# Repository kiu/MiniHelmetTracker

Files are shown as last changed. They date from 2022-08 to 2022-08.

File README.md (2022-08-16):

# MiniHelmetTracker

*MiniHelmetTracker* is a real-time standings table robot.

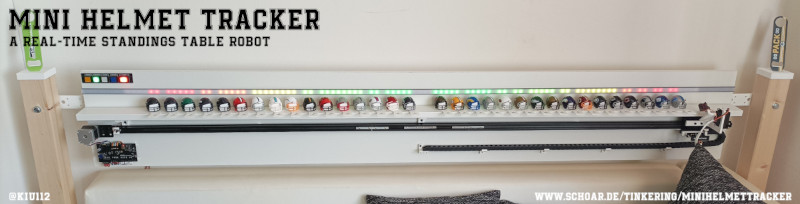
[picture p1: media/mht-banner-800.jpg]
MHT

 
*MiniHelmetTracker* retrieves standings data - close to real-time - via WiFi and sorts [mini helmets](https://www.amazon.de/Riddell-8056173-NFL-32-teiliges-Helm-Tracker-Set/dp/B088W86SX4/) by league, conference, division or playoffs. A physical representation of the well known standings tables from [NFL](https://www.espn.com/nfl/standings) or [ESPN](https://www.espn.com/nfl/standings).

Checkout the [full story](https://schoar.de/tinkering/MiniHelmetTracker) or explore this repository including STL files, schematics, PCB layouts, firmware, server, etc.

# Youtube

MHT Video (https://youtu.be/LY5VMEqtx_c "MHT Video")

MHT Making (https://youtu.be/Ac1G4HAgR_Y "MHT Making")

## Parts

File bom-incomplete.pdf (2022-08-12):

BOM

Page 1

Symbol | Description | Req | +VAT | Price | Price (sum) | Provider | ID
| | | | MOQ 1
Electrical
- | TMC2209 Module | 1 | 0 | 4,94 € | 4,94 € | https://aliexpress.com | 33029587820
- | ESP8266 Module | 1 | 0 | 6,49 € | 6,49 € | https://amazon.de | B078J7LDLY
- | Power Supply 5V/12V 65W (totally overpowered) | 1 | 0 | 20,87 € | 20,87 € | https://reichelt.de | SNT RD 65A
- | Power Supply Protection | 1 | 0 | 0,44 € | 0,44 € | https://reichelt.de | TBC-07
- | Power Cord 3m | 1 | 0 | 3,90 € | 3,90 € | https://reichelt.de | NKS 300 WS
- | NEMA 17 17HS4401 | 1 | 0 | 10,96 € | 10,96 € | https://amazon.de | B07GLKQYWJ
- | Limit Switch | 1 | 0 | 2,77 € | 2,77 € | https://aliexpress.com | 1005003536527857
- | LED strip RGB APA102 60/m | 2 | 0 | 9,02 € | 18,04 € | https://aliexpress.com | 1005002583856530
| Button Square | 4 | 0 | 2,07 € | 8,28 € | https://aliexpress.com | 32886794895
| Button Rectangle | 1 | 0 | 2,06 € | 2,06 € | https://aliexpress.com | 32871885629
Mechanical
- | LED strip mount 2000x17x7 | 1 | 0 | 19,97 € | 19,97 € | https://amazon.de | B07549D36V
- | Cable Chain 10x10 (2m) | 2 | 0 | 8,06 € | 16,12 € | https://aliexpress.com | 1005001795469984
- | 2020 V-Profile 800mm | 2 | 0 | 8,57 € | 17,14 € | https://aliexpress.com | 32956797126
- | 2020 V-Profile 300mm | 1 | 0 | 5,42 € | 5,42 € | https://aliexpress.com | 32956797126
- | (4x) Pofile Connector | 2 | 0 | 5,59 € | 11,18 € | https://aliexpress.com | 33014820100
- | NEMA 17 Mounting Plate | 1 | 0 | 2,61 € | 2,61 € | https://aliexpress.com | 33012021651
- | Belt Tensioner | 1 | 0 | 6,41 € | 6,41 € | https://aliexpress.com | 4000598324722
- | GT2 Belt 5m 6mm | 1 | 0 | 4,73 € | 4,73 € | https://aliexpress.com | 32882998299
- | 2020 V-Profile gantry | 1 | 0 | 7,95 € | 7,95 € | https://aliexpress.com | 4000177053846
- | Pulley 20T W6 B4 | 1 | 0 | 1,45 € | 1,45 € | https://aliexpress.com | 4001058371220
- | Servo MG996R | 1 | 0 | 12,89 € | 12,89 € | https://amazon.de | B088NJRFD7
- | Servo MG90S | 1 | 0 | 6,89 € | 6,89 € | https://amazon.de | B095YXMG3F
Misc
- | Mini Helmet Set | 1 | 0 | 47,92 € | 47,92 € | https://amazon.de | B088W86SX4
- | Wood 2000x300x16 | 1 | 0 | 10,99 € | 10,99 € | https://obi.de | 6848618
- | Wood 70x70x2100 | 2 | 0 | 25,17 € | 50,34 € | https://obi.de | 6870299
- | Wood 58x16x2400 | 1 | 0 | 13,99 € | 13,99 € | https://obi.de | 7930035
- | PCB + Shipping jlcpcb.com | 1 | 0 | 58,11 € | 58,11 € | https://jlcpcb.com | -
- | Shipping reichelt.de | 1 | 0 | 5,95 € | 5,95 € | https://reichelt.de | -

SUM
378,81 €
378,81 €

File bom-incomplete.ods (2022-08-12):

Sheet: BOM
Symbol | Description | Req | +VAT | Price | Price (sum) | Provider | ID
 |  |  |  | MOQ | 1
Electrical
- | TMC2209 Module | 1 | 0 | 4,94 € | 4,94 € | https://aliexpress.com | 33029587820
- | ESP8266 Module | 1 | 0 | 6,49 € | 6,49 € | https://amazon.de | B078J7LDLY
- | Power Supply 5V/12V 65W (totally overpowered) | 1 | 0 | 20,87 € | 20,87 € | https://reichelt.de | SNT RD 65A
- | Power Supply Protection | 1 | 0 | 0,44 € | 0,44 € | https://reichelt.de | TBC-07
- | Power Cord 3m | 1 | 0 | 3,90 € | 3,90 € | https://reichelt.de | NKS 300 WS
- | NEMA 17 17HS4401 | 1 | 0 | 10,96 € | 10,96 € | https://amazon.de | B07GLKQYWJ
- | Limit Switch | 1 | 0 | 2,77 € | 2,77 € | https://aliexpress.com | 1005003536527857
- | LED strip RGB APA102 60/m | 2 | 0 | 9,02 € | 18,04 € | https://aliexpress.com | 1005002583856530
 | Button Square | 4 | 0 | 2,07 € | 8,28 € | https://aliexpress.com | 32886794895
 | Button Rectangle | 1 | 0 | 2,06 € | 2,06 € | https://aliexpress.com | 32871885629
Mechanical
- | LED strip mount 2000x17x7 | 1 | 0 | 19,97 € | 19,97 € | https://amazon.de | B07549D36V
- | Cable Chain 10x10 (2m) | 2 | 0 | 8,06 € | 16,12 € | https://aliexpress.com | 1005001795469984
- | 2020 V-Profile 800mm | 2 | 0 | 8,57 € | 17,14 € | https://aliexpress.com | 32956797126
- | 2020 V-Profile 300mm | 1 | 0 | 5,42 € | 5,42 € | https://aliexpress.com | 32956797126
- | (4x) Pofile Connector | 2 | 0 | 5,59 € | 11,18 € | https://aliexpress.com | 33014820100
- | NEMA 17 Mounting Plate | 1 | 0 | 2,61 € | 2,61 € | https://aliexpress.com | 33012021651
- | Belt Tensioner | 1 | 0 | 6,41 € | 6,41 € | https://aliexpress.com | 4000598324722
- | GT2 Belt 5m 6mm | 1 | 0 | 4,73 € | 4,73 € | https://aliexpress.com | 32882998299
- | 2020 V-Profile gantry | 1 | 0 | 7,95 € | 7,95 € | https://aliexpress.com | 4000177053846
- | Pulley 20T W6 B4 | 1 | 0 | 1,45 € | 1,45 € | https://aliexpress.com | 4001058371220
- | Servo MG996R | 1 | 0 | 12,89 € | 12,89 € | https://amazon.de | B088NJRFD7
- | Servo MG90S | 1 | 0 | 6,89 € | 6,89 € | https://amazon.de | B095YXMG3F
Misc
- | Mini Helmet Set | 1 | 0 | 47,92 € | 47,92 € | https://amazon.de | B088W86SX4
- | Wood 2000x300x16 | 1 | 0 | 10,99 € | 10,99 € | https://obi.de | 6848618
- | Wood 70x70x2100 | 2 | 0 | 25,17 € | 50,34 € | https://obi.de | 6870299
- | Wood 58x16x2400 | 1 | 0 | 13,99 € | 13,99 € | https://obi.de | 7930035
- | PCB + Shipping jlcpcb.com | 1 | 0 | 58,11 € | 58,11 € | https://jlcpcb.com | -
- | Shipping reichelt.de | 1 | 0 | 5,95 € | 5,95 € | https://reichelt.de | -
 |  |  |  |  | SUM
 |  |  |  |  | 378,81 €
 |  |  |  |  | 378,81 €

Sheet: BOM_2
Symbol | Description | Req | +VAT | Price | Price (sum) | Provider | ID
 |  |  |  | MOQ | 1
Electronic / Base
 | ATMEGA 328PB-AU | 1 | 0 | 1,44 € | 1,44 € | http://reichelt.de | ATMEGA 328PB-AU
 | LDO 5V >=200mA | 1 | 0 | 0,36 € | 0,36 € | http://reichelt.de | NCP 1117 ST50T3G
 | NPN Transitor >=100mA | 1 | 0 | 0,02 € | 0,02 € | http://reichelt.de | BC 847C SMD
 | Diode | 1 | 0 | 0,02 € | 0,02 € | http://reichelt.de | BAV 99 SMD
 | 10uF/25V Tantalum D | 2 | 0 | 0,35 € | 0,70 € | http://reichelt.de | TAJ 7343 10/25
 | 100nF 0805 | 3 | 0 | 0,05 € | 0,15 € | http://reichelt.de | KEM X7R0805 100N
 | 10k 0805 | 3 | 0 | 0,02 € | 0,06 € | http://reichelt.de | RND 0805 1 10K
 | 1k 0805 | 1 | 0 | 0,02 € | 0,02 € | http://reichelt.de | RND 0805 1 1,0K
 | Relay 5V | 1 | 0 | 2,60 € | 2,60 € | http://reichelt.de | G2RL-24 DC5
 | 1x05 Pin Header with cable | 2 | 0 | 0,67 € | 1,34 € | http://reichelt.de | PS 25/5G BR
 | Terminal 1x02 5.08 | 2 | 0 | 0,25 € | 0,50 € | http://reichelt.de | CTB0509-2
 | Header 2x03 2.54 | 1 | 0 | 0,25 € | 0,25 € | http://reichelt.de | WSL 6G
 | Header 1x02 2.54 | 1 | 0 | 0,05 € | 0,05 € | http://reichelt.de | MPE 087-1-002
 | Header 1x03 2.54 | 1 | 0 | 0,08 € | 0,08 € | http://reichelt.de | MPE 087-1-003
 | Socket 1x05 2.54 | 1 | 0 | 0,23 € | 0,23 € | http://reichelt.de | MPE 094-1-005
 | Socket 1x04 2.54 | 1 | 0 | 0,17 € | 0,17 € | http://reichelt.de | MPE 094-1-004
Electronic / Gantry
 | ATMEGA 328PB-AU | 1 | 0 | 1,44 € | 1,44 € | http://reichelt.de | ATMEGA 328PB-AU
 | LDO 5V >=200mA | 1 | 0 | 0,36 € | 0,36 € | http://reichelt.de | NCP 1117 ST50T3G
 | NPN Transitor >=100mA | 1 | 0 | 0,02 € | 0,02 € | http://reichelt.de | BC 847C SMD
 | Diode | 1 | 0 | 0,02 € | 0,02 € | http://reichelt.de | BAV 99 SMD
 | 10uF/25V Tantalum D | 2 | 0 | 0,35 € | 0,70 € | http://reichelt.de | TAJ 7343 10/25
 | Belt Tensioner | 1
 | T-Nut M4 (?) | 4
 | M4x?? | 4
 | GT2 Belt 5m | 1
Electronic / Control
Electrical
 | Power Supply 1x5V 1x12V | 1
 | Power Supply Protection | 1
 | Power Cord | 1
 | Cable Chain 10x10 (3m) | 3
Mechanical
 | 2020 V-Profile 800mm | 2
 | 2020 V-Profile 400mm | 1
 | Pofile Connector (4) | 4
 | NEMA 17 Mounting Plate | 1
 | Belt Tensioner | 1
 | T-Nut M4 (?) | 4
 | M4x?? | 4
 | GT2 Belt 5m | 1
 | Gantry | 1
- | Power Supply 15V >=2A | 1 | 0 | 11,07 € | 11,07 € | http://reichelt.de | MW LRS-35-15
- | Power Supply Protection | 1 | 0 | 0,34 € | 0,34 € | http://reichelt.de | TBC-05
- | Case 167x125x82mm | 1 | 0 | 10,10 € | 10,10 € | http://reichelt.de | HNS 12516782-H01
- | Cable 2x0,75mm 5m | 1 | 0 | 1,30 € | 1,30 € | http://reichelt.de | LAT 275-5
- | Connector | 1 | 0 | 1,30 € | 1,30 € | http://reichelt.de | DELOCK 65421
- | Separator M3 10mm | 2 | 0 | 0,11 € | 0,22 € | http://reichelt.de | DI 10MM
- | Separator M4 5mm | 3 | 0 | 0,09 € | 0,27 € | http://reichelt.de | VT DKM 5MM
- | Cable Gland M16 | 2 | 0 | 0,25 € | 0,50 € | http://reichelt.de | MBF 16
- | Cable Gland M16 Fix | 2 | 0 | 0,10 € | 0,20 € | http://reichelt.de | MGM 16
- | Aderendhülsen 0,75mm | 1 | 0 | 1,03 € | 1,03 € | http://reichelt.de | VT AEHI 0,75-100
- | Shipping reichelt.de | 1 | 0 | 5,95 € | 5,95 € | http://reichelt.de | -
Misc
(JHTU21) | GY-21 HTU21 Temperature Module | 1 | 0 | 5,99 € | 5,99 € | http://amazon.de | B07V9PJP1K
(JRTC1) | DS3231 RTC Module | 1 | 0 | 10,89 € | 10,89 € | http://amazon.de | B07QW2D4NF
- | Screw M3x5 | 4 | 0 | 0,00 € | 0,00 € | - | -
- | Screw M4x14 | 3 | 0 | 0,00 € | 0,00 € | - | -
(JNOW1, JWAIT1) | Push Button, 19mm, LED Red + Blue | 2 | 0 | 3,60 € | 7,20 € | http://aliexpress.com | 1005002351204813
- | PCB 138x85 + Stencil + Shipping + VAT | 1 | 0 | 37,33 € | 37,33 € | http://jlcpcb.com | -
 |  |  |  |  | SUM
 |  |  |  |  | 104,22 €
 |  |  |  |  | 104,22 €

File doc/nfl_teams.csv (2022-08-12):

ID | Name | Abbreviation | Conference | Division
1 | Arizona Cardinals | ARI | NFC | West
2 | Atlanta Falcons | ATL | NFC | South
3 | Baltimore Ravens | BAL | AFC | North
4 | Buffalo Bills | BUF | AFC | East
5 | Carolina Panthers | CAR | NFC | South
6 | Chicago Bears | CHI | NFC | North
7 | Cincinnati Bengals | CIN | AFC | North
8 | Cleveland Browns | CLE | AFC | North
9 | Dallas Cowboys | DAL | NFC | East
10 | Denver Broncos | DEN | AFC | West
11 | Detroit Lions | DET | NFC | North
12 | Green Bay Packers | GB | NFC | North
13 | Houston Texans | HOU | AFC | South
14 | Indianapolis Colts | IND | AFC | South
15 | Jacksonville Jaguars | JAX | AFC | South
16 | Kansas City Chiefs | KC | AFC | West
17 | Miami Dolphins | MIA | AFC | East
18 | Minnesota Vikings | MIN | NFC | North
19 | New England Patriots | NE | AFC | East
20 | New Orleans Saints | NO | NFC | South
21 | NY Giants | NYG | NFC | East
22 | NY Jets | NYJ | AFC | East
23 | Las Vegas Raiders | LV | AFC | West
24 | Philadelphia Eagles | PHI | NFC | East
25 | Pittsburgh Steelers | PIT | AFC | North
26 | Los Angeles Chargers | LAC | AFC | West
27 | San Francisco 49ers | SF | NFC | West
28 | Seattle Seahawks | SEA | NFC | West
29 | Los Angeles Rams | LAR | NFC | West
30 | Tampa Bay Buccaneers | TB | NFC | South
31 | Tennessee Titans | TEN | AFC | South
32 | Washington Football Team | WAS | NFC | East

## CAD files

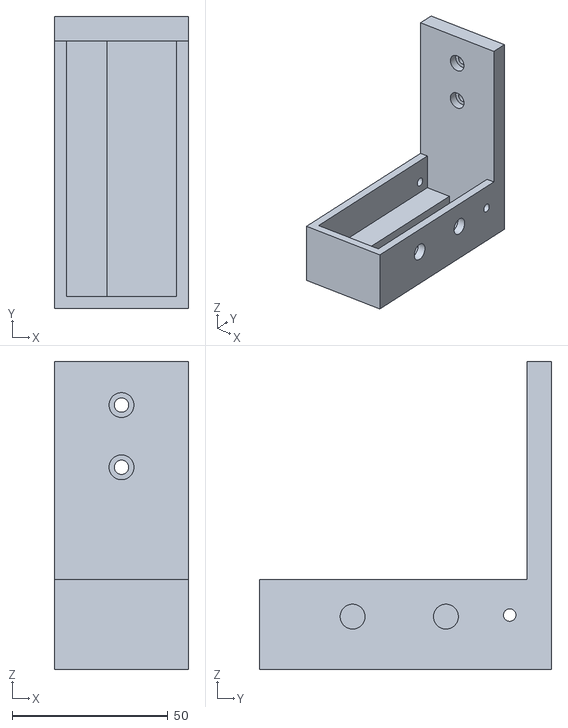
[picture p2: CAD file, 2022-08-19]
mech/mount-meanwell-35W.stl
43.2 x 94.0 x 99.0

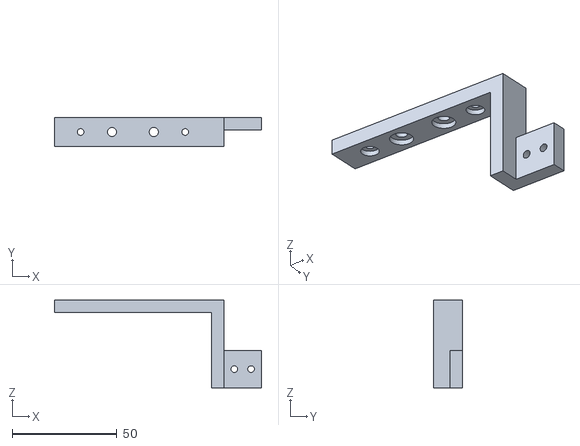
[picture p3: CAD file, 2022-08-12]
mech/chain-end.stl
99.0 x 14.0 x 42.0

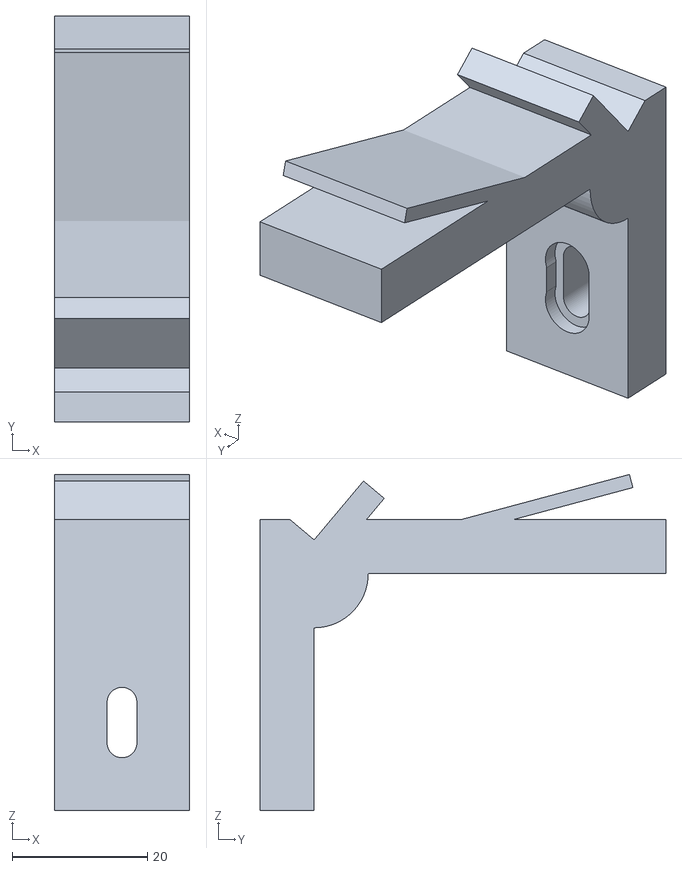
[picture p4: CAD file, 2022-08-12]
mech/mount-plate_3x.stl
20.0 x 60.0 x 49.7

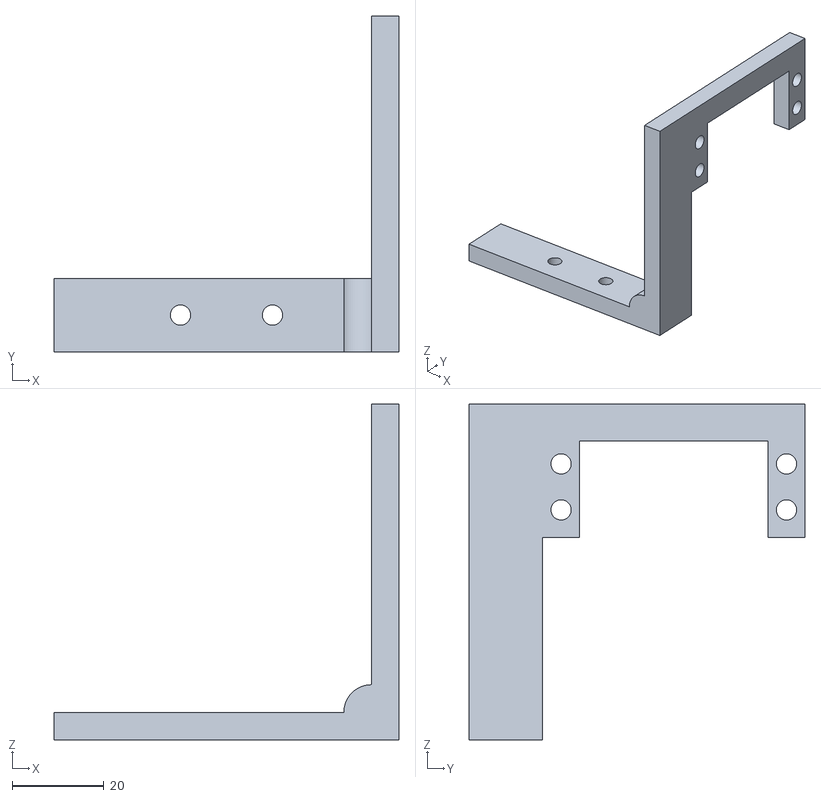
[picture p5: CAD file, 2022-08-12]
mech/mount-servo.stl
75.0 x 73.0 x 73.0

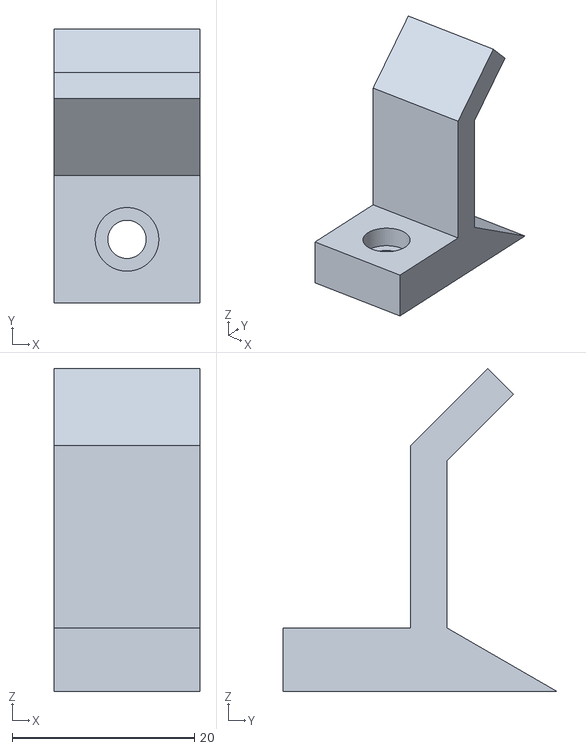
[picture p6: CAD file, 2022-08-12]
mech/chain-middle_4x.stl
16.0 x 30.1 x 35.5

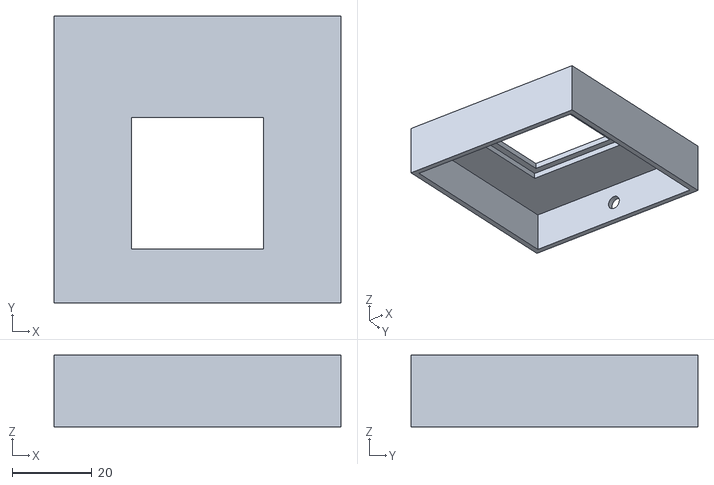
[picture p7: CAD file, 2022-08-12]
mech/mount-opener-base_2x.stl
72.0 x 72.0 x 18.0

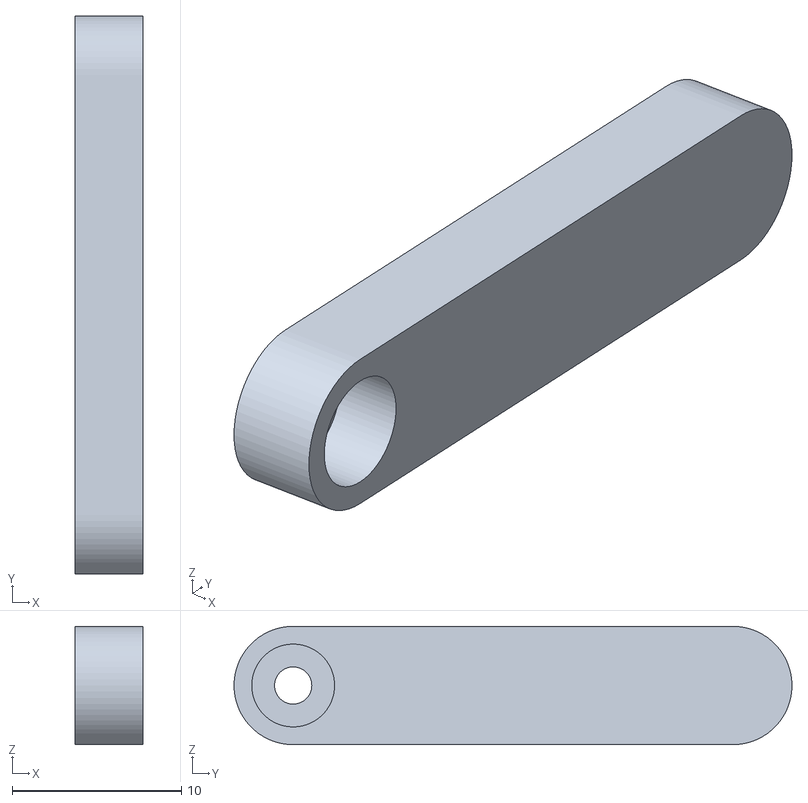
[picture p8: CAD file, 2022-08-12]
mech/helmet-horn.stl
4.00 x 33.0 x 7.00

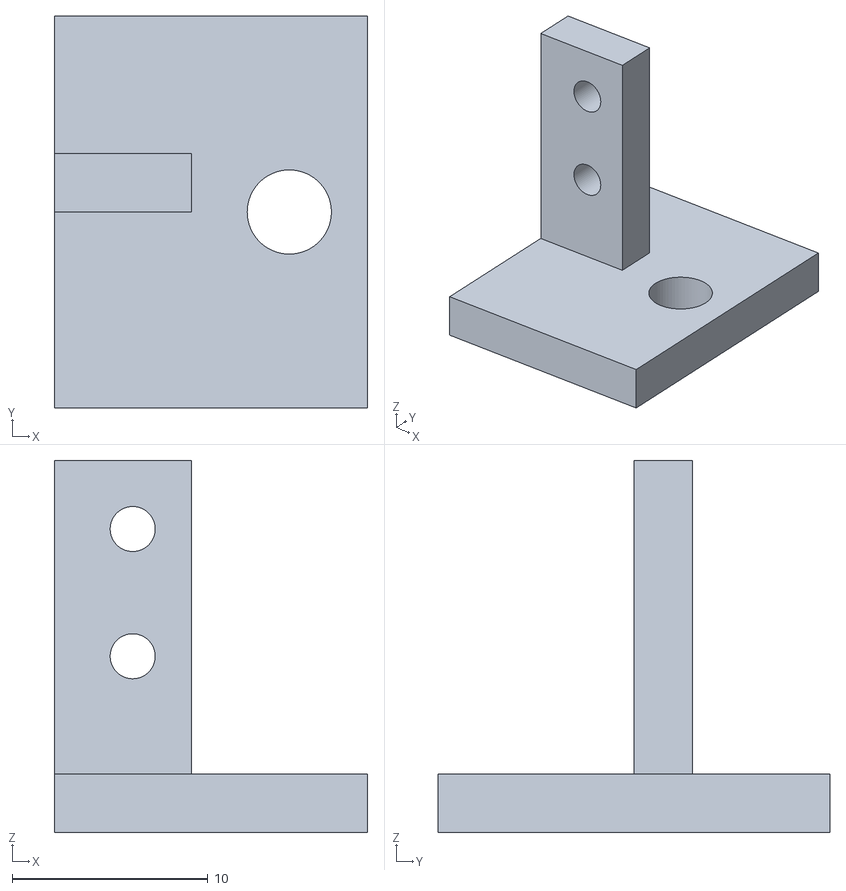
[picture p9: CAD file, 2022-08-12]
mech/mount-limit_switch.stl
16.0 x 20.0 x 19.0

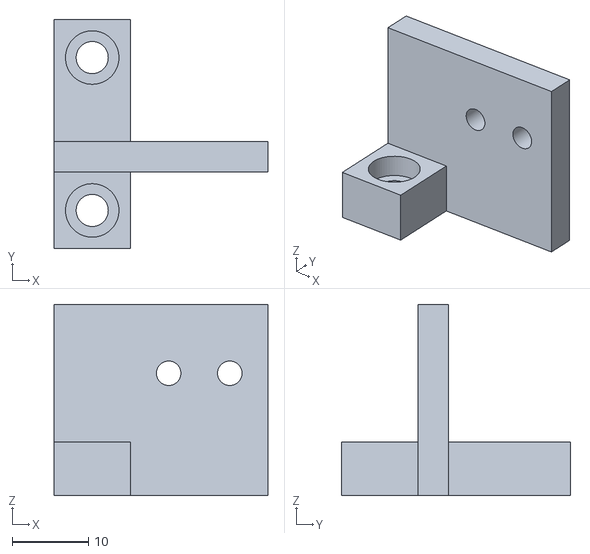
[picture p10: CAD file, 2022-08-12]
mech/chain-start.stl
28.0 x 30.0 x 25.0

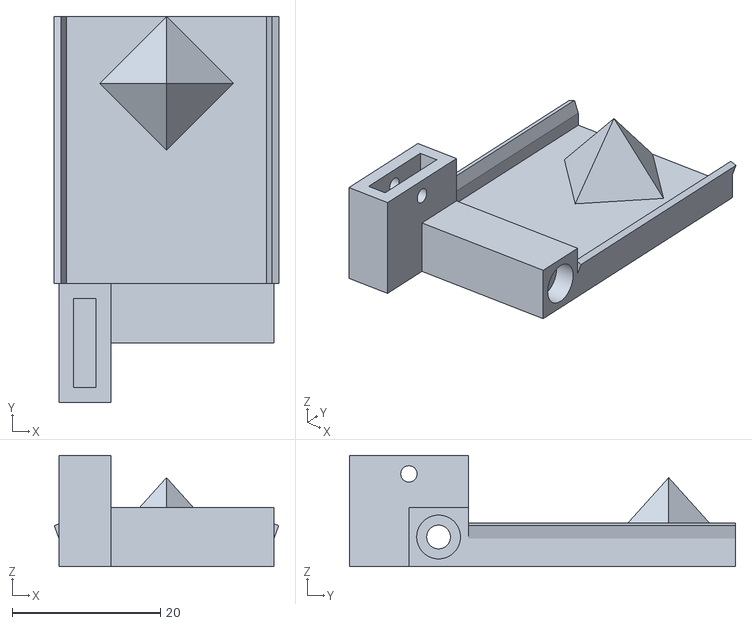
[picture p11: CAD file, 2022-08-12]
mech/helmet-receptacle.stl
30.2 x 52.0 x 15.0

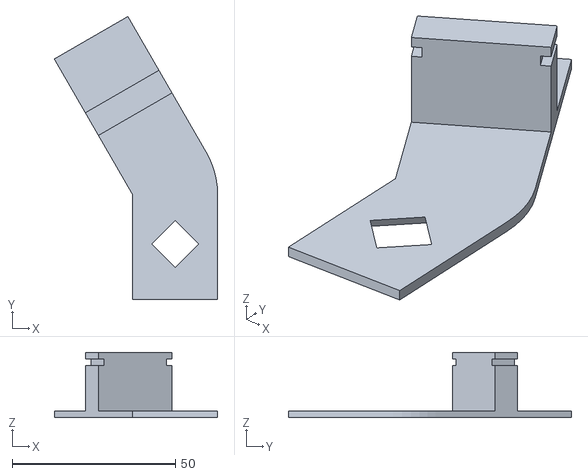
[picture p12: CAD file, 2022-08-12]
mech/helmet-holder_32x.stl
50.0 x 86.6 x 20.0

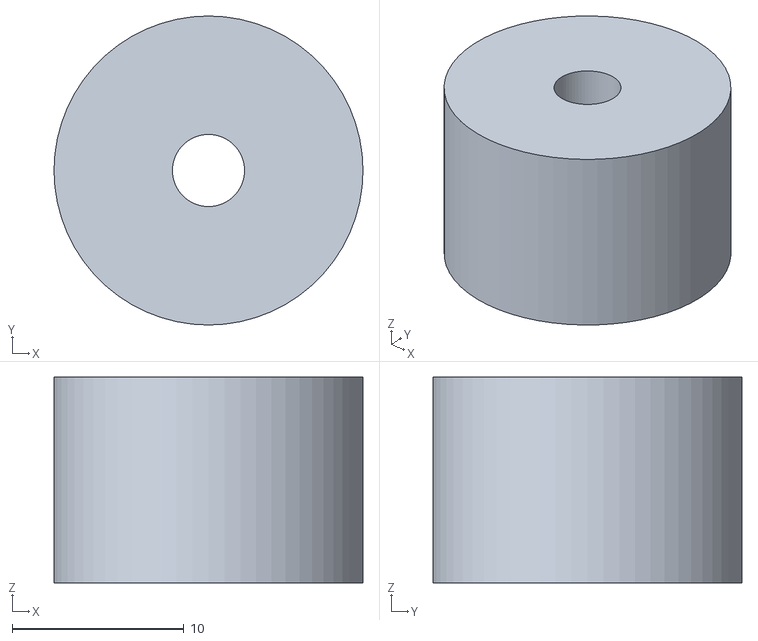
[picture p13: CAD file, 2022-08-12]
mech/mount-rail_2x.stl
18.0 x 18.0 x 12.0

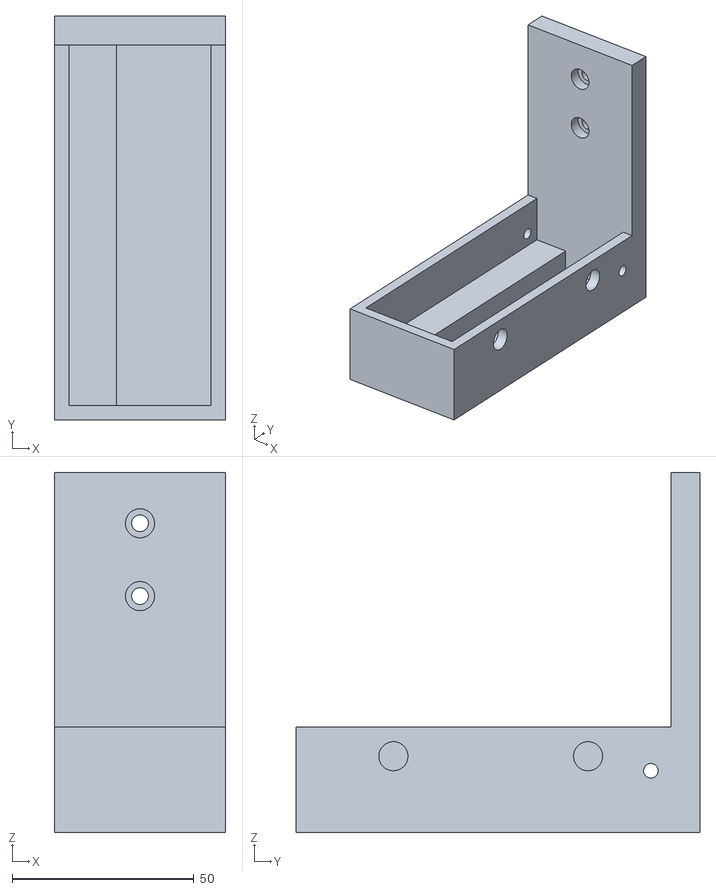
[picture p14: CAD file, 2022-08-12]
mech/mount-meanwell.stl
47.0 x 111.0 x 99.0

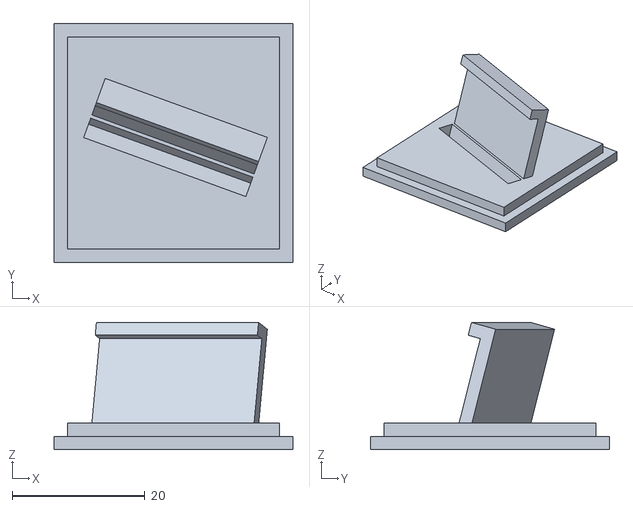
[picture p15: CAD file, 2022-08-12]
mech/mount-opener-right.stl
36.0 x 36.0 x 19.2

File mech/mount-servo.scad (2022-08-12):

$fn = 60;

//--------------------------------------------------------

	  w = 75;
	  b = 16;
	  difference() {
			cube([w, b, 6]);
			translate([w/2 - 20 / 2, b/2, 0]) cylinder(h=6, d=4.4);
			translate([w/2 - 20 / 2, b/2, 0]) cylinder(h=2, d=9);
			
			translate([w/2 + 20 / 2, b/2, 0]) cylinder(h=6, d=4.4);
			translate([w/2 + 20 / 2, b/2, 0]) cylinder(h=2, d=9);
	  }
	  
	  translate([w - 6, 0, 0]) cube([6, b, 6 + 50-11+29-1]);
	  translate([w - 6, b/2, 6]) rotate([90, 0, 0]) cylinder(h = b, d = 12, center = true);

translate([75, 0+16, 6 + 50+29-11-1]) rotate([-90, 0, 90]) difference() {
	  cube([41+16, 21+8, 6]);
	  translate([8, 8, 0]) cube([41, 21, 6]);
	  translate([4, 8+5, 0]) cylinder(h=6, d=4.4);
	  translate([4, 8++5+10, 0]) cylinder(h=6, d=4.4);
	  translate([41 + 8 + 4, 8+5, 0]) cylinder(h=6, d=4.4);
	  translate([41 + 8 + 4, 8+5+10, 0]) cylinder(h=6, d=4.4);
}

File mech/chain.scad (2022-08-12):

$fn = 60;

//--------------------------------------------------------

translate([0, 0, 0]) start();
translate([40, 0, 0]) middle();
translate([80, 0, 0]) end();

//--------------------------------------------------------

module start() {
	  difference() {
			cube([10, 30, 7]);
			translate([10/2, 10/2, 0]) cylinder(h=7, d=4.2);
			translate([10/2, 10/2, 4]) cylinder(h=3, d=7);

			translate([10/2, 30-10/2, 0]) cylinder(h=7, d=4.2);
			translate([10/2, 30-10/2, 4]) cylinder(h=7, d=7);
	  }


	  translate([0, 10 + 4, 0]) rotate([90, 0, 0]) difference() {
			cube([10+18, 18+7, 4]);
			translate([10 + 5, 18/2+7, 0]) cylinder(h=4, d=3.2);
			translate([10 + 5 + 8, 18/2+7, 0]) cylinder(h=4, d=3.2);
	  }
}

module middle() {
	  difference() {
			cube([16, 32, 7]);
			translate([0, 12.8, 10]) rotate([-30, 0, 0]) cube([30, 30, 30]);
			translate([16/2, 7, 0]) cylinder(h=7, d=4.2);
			translate([16/2, 7, 4]) cylinder(h=3, d=7);
	  }
	  
	  translate([0, 18 - 4, 7]) cube([16, 4, 20]);
	  translate([0, 18 - 4, 27]) rotate([-45, 0, 0]) cube([16, 4, 12]);
}

module end() {
	  w = 75;
	  difference() {
			cube([w, 14, 6]);
			translate([w/2 - 20 / 2, 14/2, 0]) cylinder(h=6, d=4.4);
			translate([w/2 - 20 / 2, 14/2, 0]) cylinder(h=2, d=9);
			
			translate([w/2 + 20 / 2, 14/2, 0]) cylinder(h=6, d=4.4);
			translate([w/2 + 20 / 2, 14/2, 0]) cylinder(h=2, d=9);

			translate([w/2 - 50 / 2, 14/2, 0]) cylinder(h=6, d=3.2);
			translate([w/2 - 50 / 2, 14/2, 0]) cylinder(h=2, d=7);
			translate([w/2 + 50 / 2, 14/2, 0]) cylinder(h=6, d=3.2);
			translate([w/2 + 50 / 2, 14/2, 0]) cylinder(h=2, d=7);
	  }

	  d = 36;
	  
	  translate([w, 0, -d]) cube([6, 14, d+6]);
	  
	  translate([w + 6, 14, -d]) rotate([90, 0, 0]) difference() {
			cube([18, 18, 6]);
			translate([5, 18/2, 0]) cylinder(h=6, d=3.2);
			translate([5, 18/2, 0]) cylinder(h=2, d=6);
			translate([5 + 8, 18/2, 0]) cylinder(h=6, d=3.2);
			translate([5 + 8, 18/2, 0]) cylinder(h=2, d=6);
	  }
}

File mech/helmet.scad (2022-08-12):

$fn = 60;

base_thick = 2.0;
holder_width = 26.0;
recept_width = holder_width + 1 + 2;

height = 18;

//--------------------------------------------------------

grab();
translate ([1.5, 18, 2]) holder();
translate ([recept_width/2 - 4/2, 0, 20]) rotate([0, 90, 0]) horn();

//--------------------------------------------------------
module grab() {
	  rotate([0, 90, 0]) translate([-8, 0, 0]) servo_mount_big();	  
	  translate([0, 8, 8]) rotate([90, 0, 0]) servo_mount_small();
	  translate([0, -8, 0]) cube([7, 8, 8]);
	  translate([0, 8, 0]) receptacle();
}

//--------------------------------------------------------

module servo_mount_small() {
	  difference() {
			cube([7, 7, 16]);
			translate([2, 2, 2]) cube([3, 5, 12]);
			translate([7/2, 5/2 + 2, 16 / 2]) rotate([0, 90, 0]) cylinder(h=7, d=2.2, center = true);
	  }
}

//--------------------------------------------------------

module servo_mount_big() {
	  servo_height = recept_width;
	  servo_gear = 5.9;
	  servo_gear_height = 3.0;
	  servo_screw = 3.2;
	  servo_screw_channel = 2.0;
	  servo_screw_head = 6.4;
	  servo_block = 8;
	  
	  difference() {
			cube([servo_block, servo_block, servo_height]);
			translate([servo_block / 2, servo_block / 2, 0]) {
				  translate([0, 0, servo_height - servo_gear_height]) cylinder(h=servo_gear_height, d=servo_gear);
				  translate([0, 0, servo_height - servo_gear_height - servo_screw_channel]) cylinder(h=servo_screw_channel, d=servo_screw);
				  translate([0, 0, 0]) cylinder(h=servo_height - servo_gear_height - servo_screw_channel, d=servo_screw_head);
			}
	  }
}

//--------------------------------------------------------

module receptacle() {
	  recept_length = 36.0;
	  recept_capture = 4.0;
	  recept_empty = 6;
	  
	  cube([recept_width, recept_length, base_thick]);
	  
	  half2 = (base_thick + recept_capture) / 3 * 2;
	  half1 = (base_thick + recept_capture) / 3 * 1;
	  
	  translate([0, 0, 0]) cube([1, recept_length, half2]);
	  translate([0.06, 0, half2 - 0.35]) rotate([0, -20, 0]) cube([1, recept_length, half1]);
	  	  
	  translate([recept_width - 1, 0, 0]) cube([1, recept_length, half2]);
	  translate([recept_width - 1, 0, half2]) rotate([0, 20, 0]) cube([1, recept_length, half1]);
	  
	  h = base_thick + recept_capture + recept_empty + recept_capture;
	  translate([14.5, 27, 2]) cylinder(10,9,0,$fn=4);
}

//--------------------------------------------------------

module holder() {
difference() {
union() {
	intersection() {
	  cube([holder_width, 32+20, base_thick]);
	  translate([0, 32, 0]) rotate([0,0,30]) {
			cylinder(h=base_thick, d=holder_width*2);
			cube([holder_width, 48, base_thick]);
	  }
	}
	
	cube([holder_width, 32, base_thick]);
	translate([0, 32, 0]) rotate([0,0,30]) {
		cube([holder_width, 48, base_thick]);
		translate([0, 48-27, 0]) {
			difference() {
				  cube([holder_width, 8, 20]);
				  translate([0, 0, 20 - 2 - 2]) cube([2, holder_width, 2]);
				  translate([holder_width-2, 0, 20 - 2 - 2]) cube([2, holder_width, 2]);
			}
		}
    }
	}

translate([13, 25-8, 0]) cylinder(10,9,0,$fn=4);	
	}
}

//--------------------------------------------------------

module horn() {
	  servo_height = 4;
	  servo_gear = 4.9;
	  servo_gear_height = 3.0;
	  servo_screw = 2.2;
	  servo_screw_channel = 1.0;
	  servo_screw_head = 5;
	  servo_block = 7;
	  servo_arm = 26;
	  
	  difference() {
			union() {
				  cylinder(h=servo_height, d=servo_block);
				  translate([-servo_block / 2, 0, 0]) cube([servo_block, servo_arm, servo_height]);
				  translate([0, servo_arm, 0]) cylinder(h=servo_height, d=servo_block);
			}
			translate([0, 0, servo_height - servo_gear_height]) cylinder(h=servo_gear_height, d=servo_gear);
			translate([0, 0, servo_height - servo_gear_height - servo_screw_channel]) cylinder(h=servo_screw_channel, d=servo_screw);
			translate([0, 0, 0]) cylinder(h=servo_height - servo_gear_height - servo_screw_channel, d=servo_screw_head);
	  }
}

//--------------------------------------------------------

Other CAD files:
mech/mount-opener-left.stl
mech/mount-limit_switch.scad
mech/mount-meanwell-35W.scad
mech/mount-meanwell.scad
mech/mount-opener.scad
mech/mount-plate.scad
mech/mount-rail.scad

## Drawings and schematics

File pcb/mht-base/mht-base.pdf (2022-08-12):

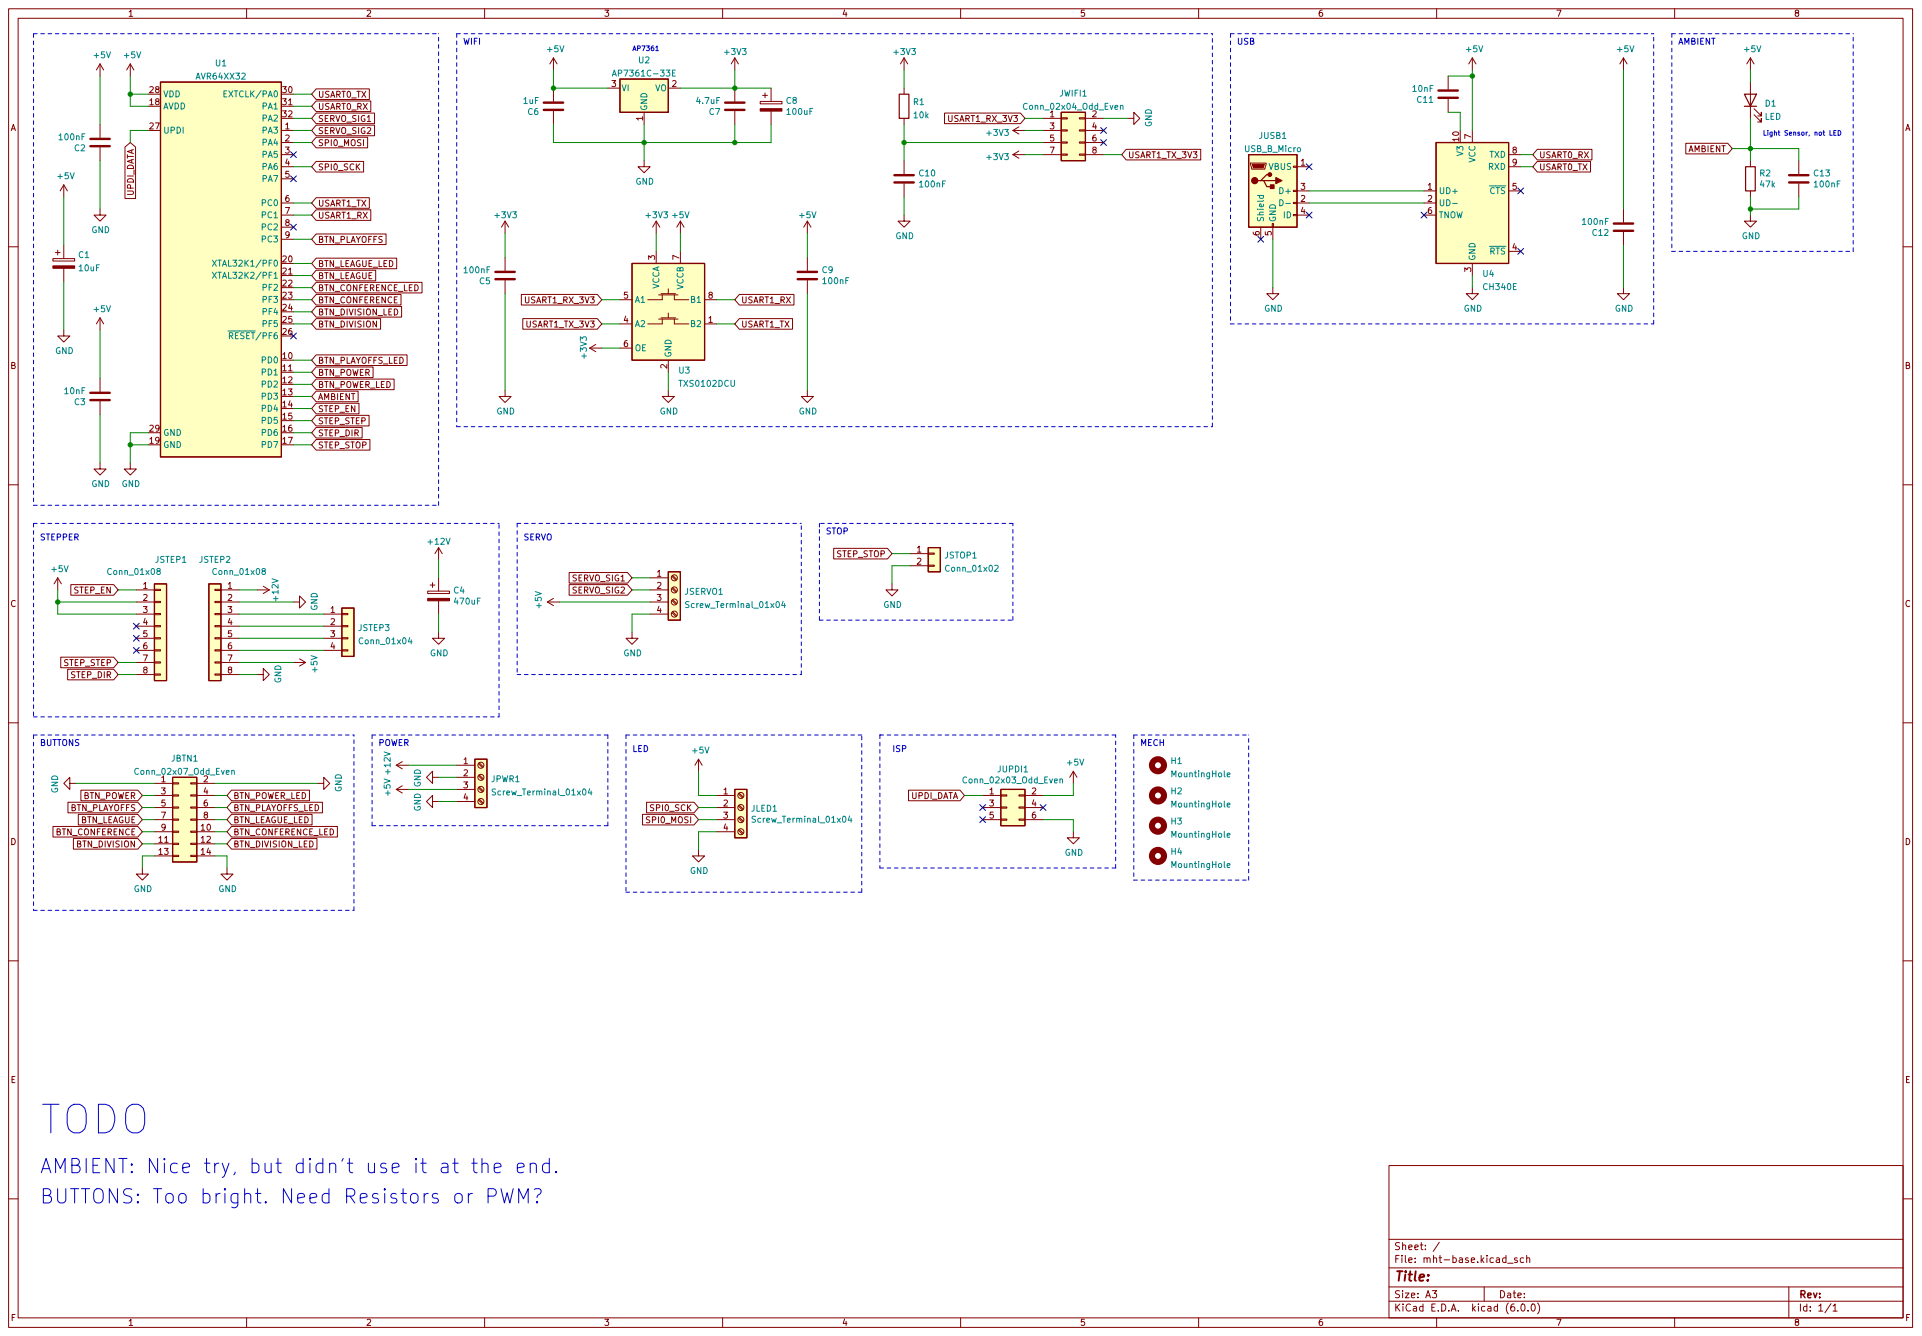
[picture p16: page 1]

Light Sensor, not LED AMBIENT

3 ~{RTS} 4 ~{CTS} 5 TNOW 6 VCC

LED BUTTONS BUTTONS: Too bright. Need Resistors or PWM?

AMBIENT: Nice try, but didn't use it at the end.

File: mht-base.kicad_sch Sheet: /

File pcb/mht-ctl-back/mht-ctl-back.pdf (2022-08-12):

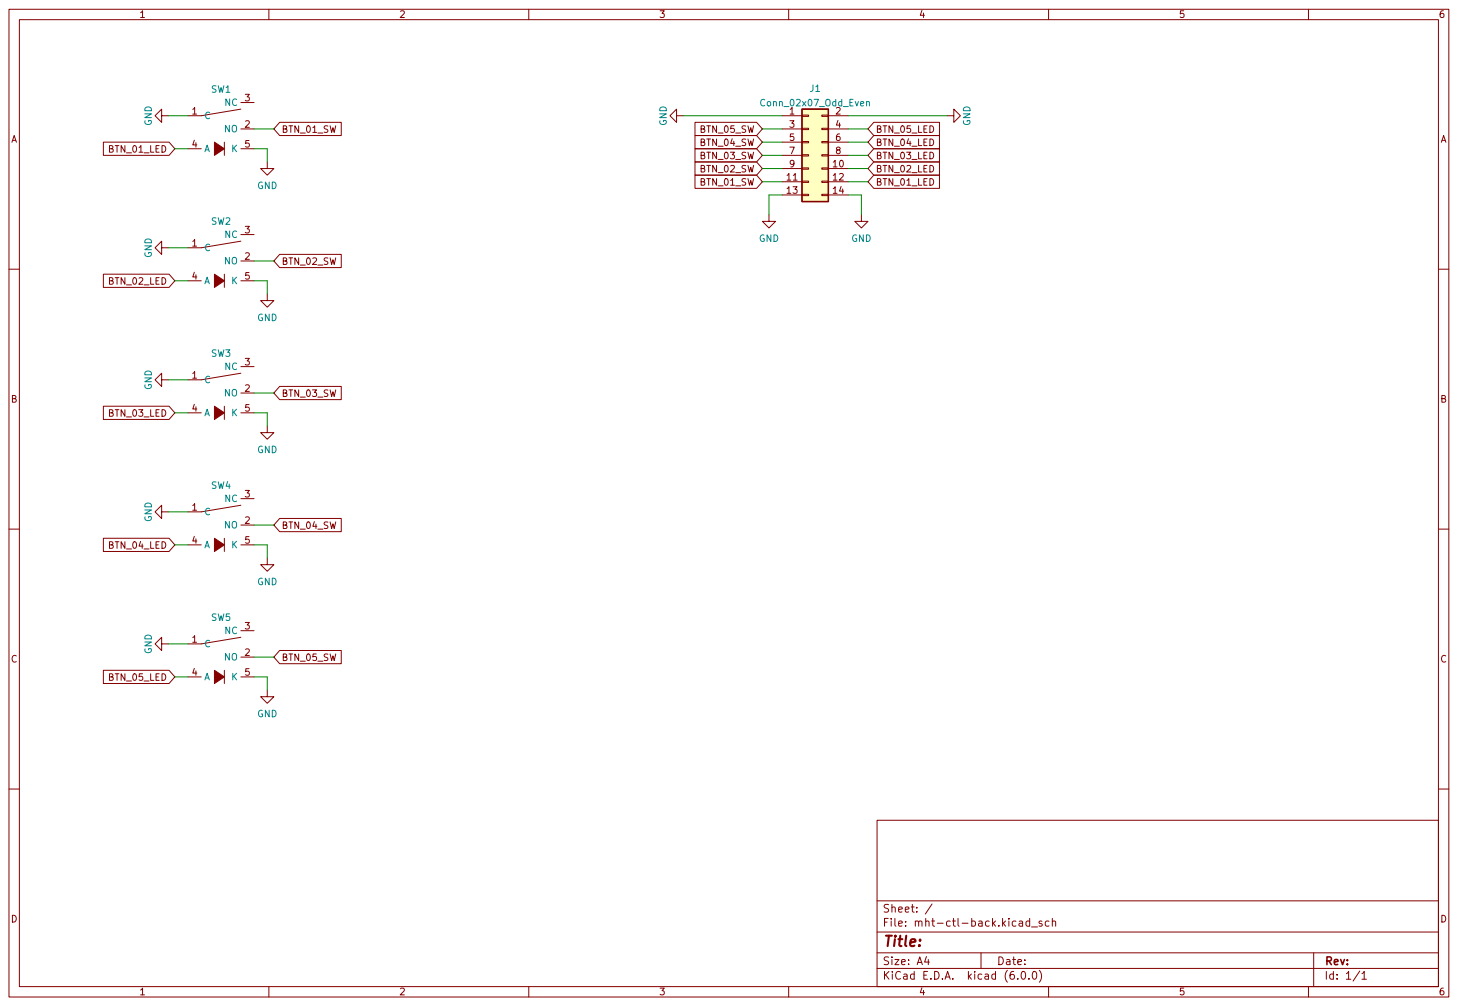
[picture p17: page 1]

File: mht-ctl-back.kicad_sch Sheet: /

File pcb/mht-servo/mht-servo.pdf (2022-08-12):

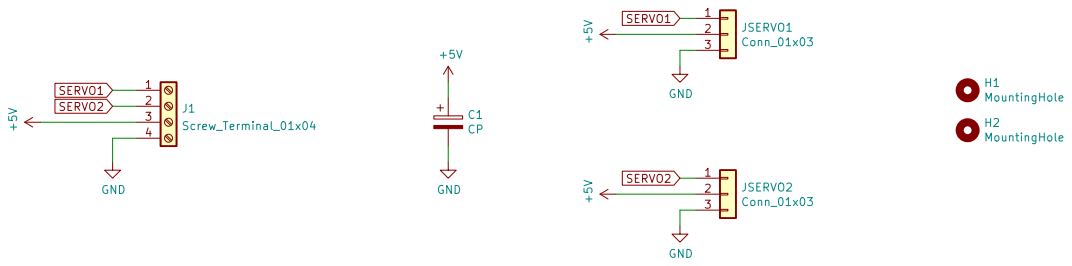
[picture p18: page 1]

File: mht-servo.kicad_sch Sheet: /
Id: 1/1 Title:

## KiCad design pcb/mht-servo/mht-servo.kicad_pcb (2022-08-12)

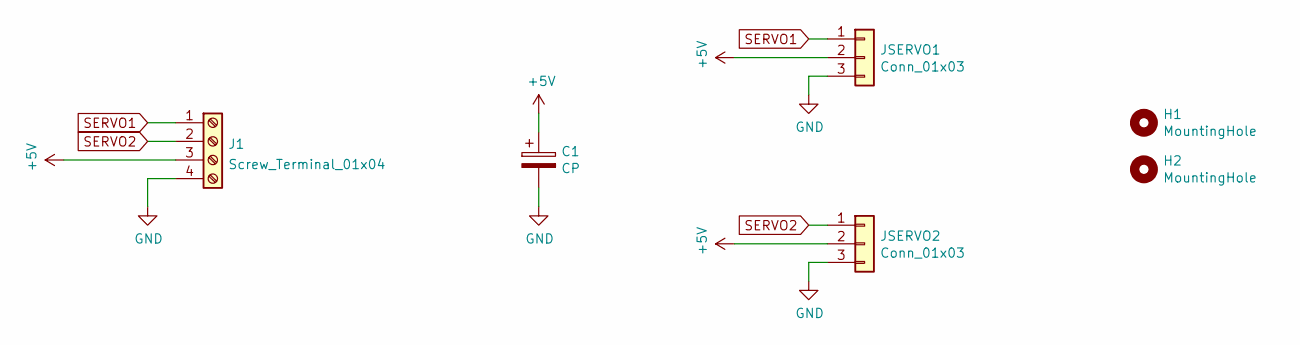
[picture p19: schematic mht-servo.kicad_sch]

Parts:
C1: CP; CP_Elec_8x10
H1, H2: MountingHole; MountingHole_3.2mm_M3
J1: Screw_Terminal_01x04; PinHeader_1x04_P2.54mm_Vertical
JSERVO1, JSERVO2: Conn_01x03; Pin_Header_Straight_1x03_Pitch2.54mm

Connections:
+5V: C1.1, J1.3, JSERVO1.2, JSERVO2.2
GND: C1.2, J1.4, JSERVO1.3, JSERVO2.3
SERVO1: J1.1, JSERVO1.1
SERVO2: J1.2, JSERVO2.1

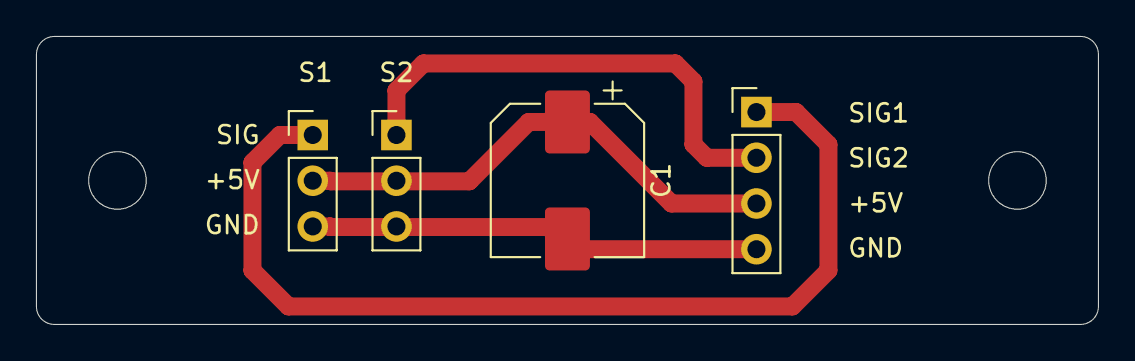
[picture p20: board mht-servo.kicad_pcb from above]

Board: 2 copper layers, 59.0 x 16.0 mm, 6 parts (0 on the bottom side), 4 nets.

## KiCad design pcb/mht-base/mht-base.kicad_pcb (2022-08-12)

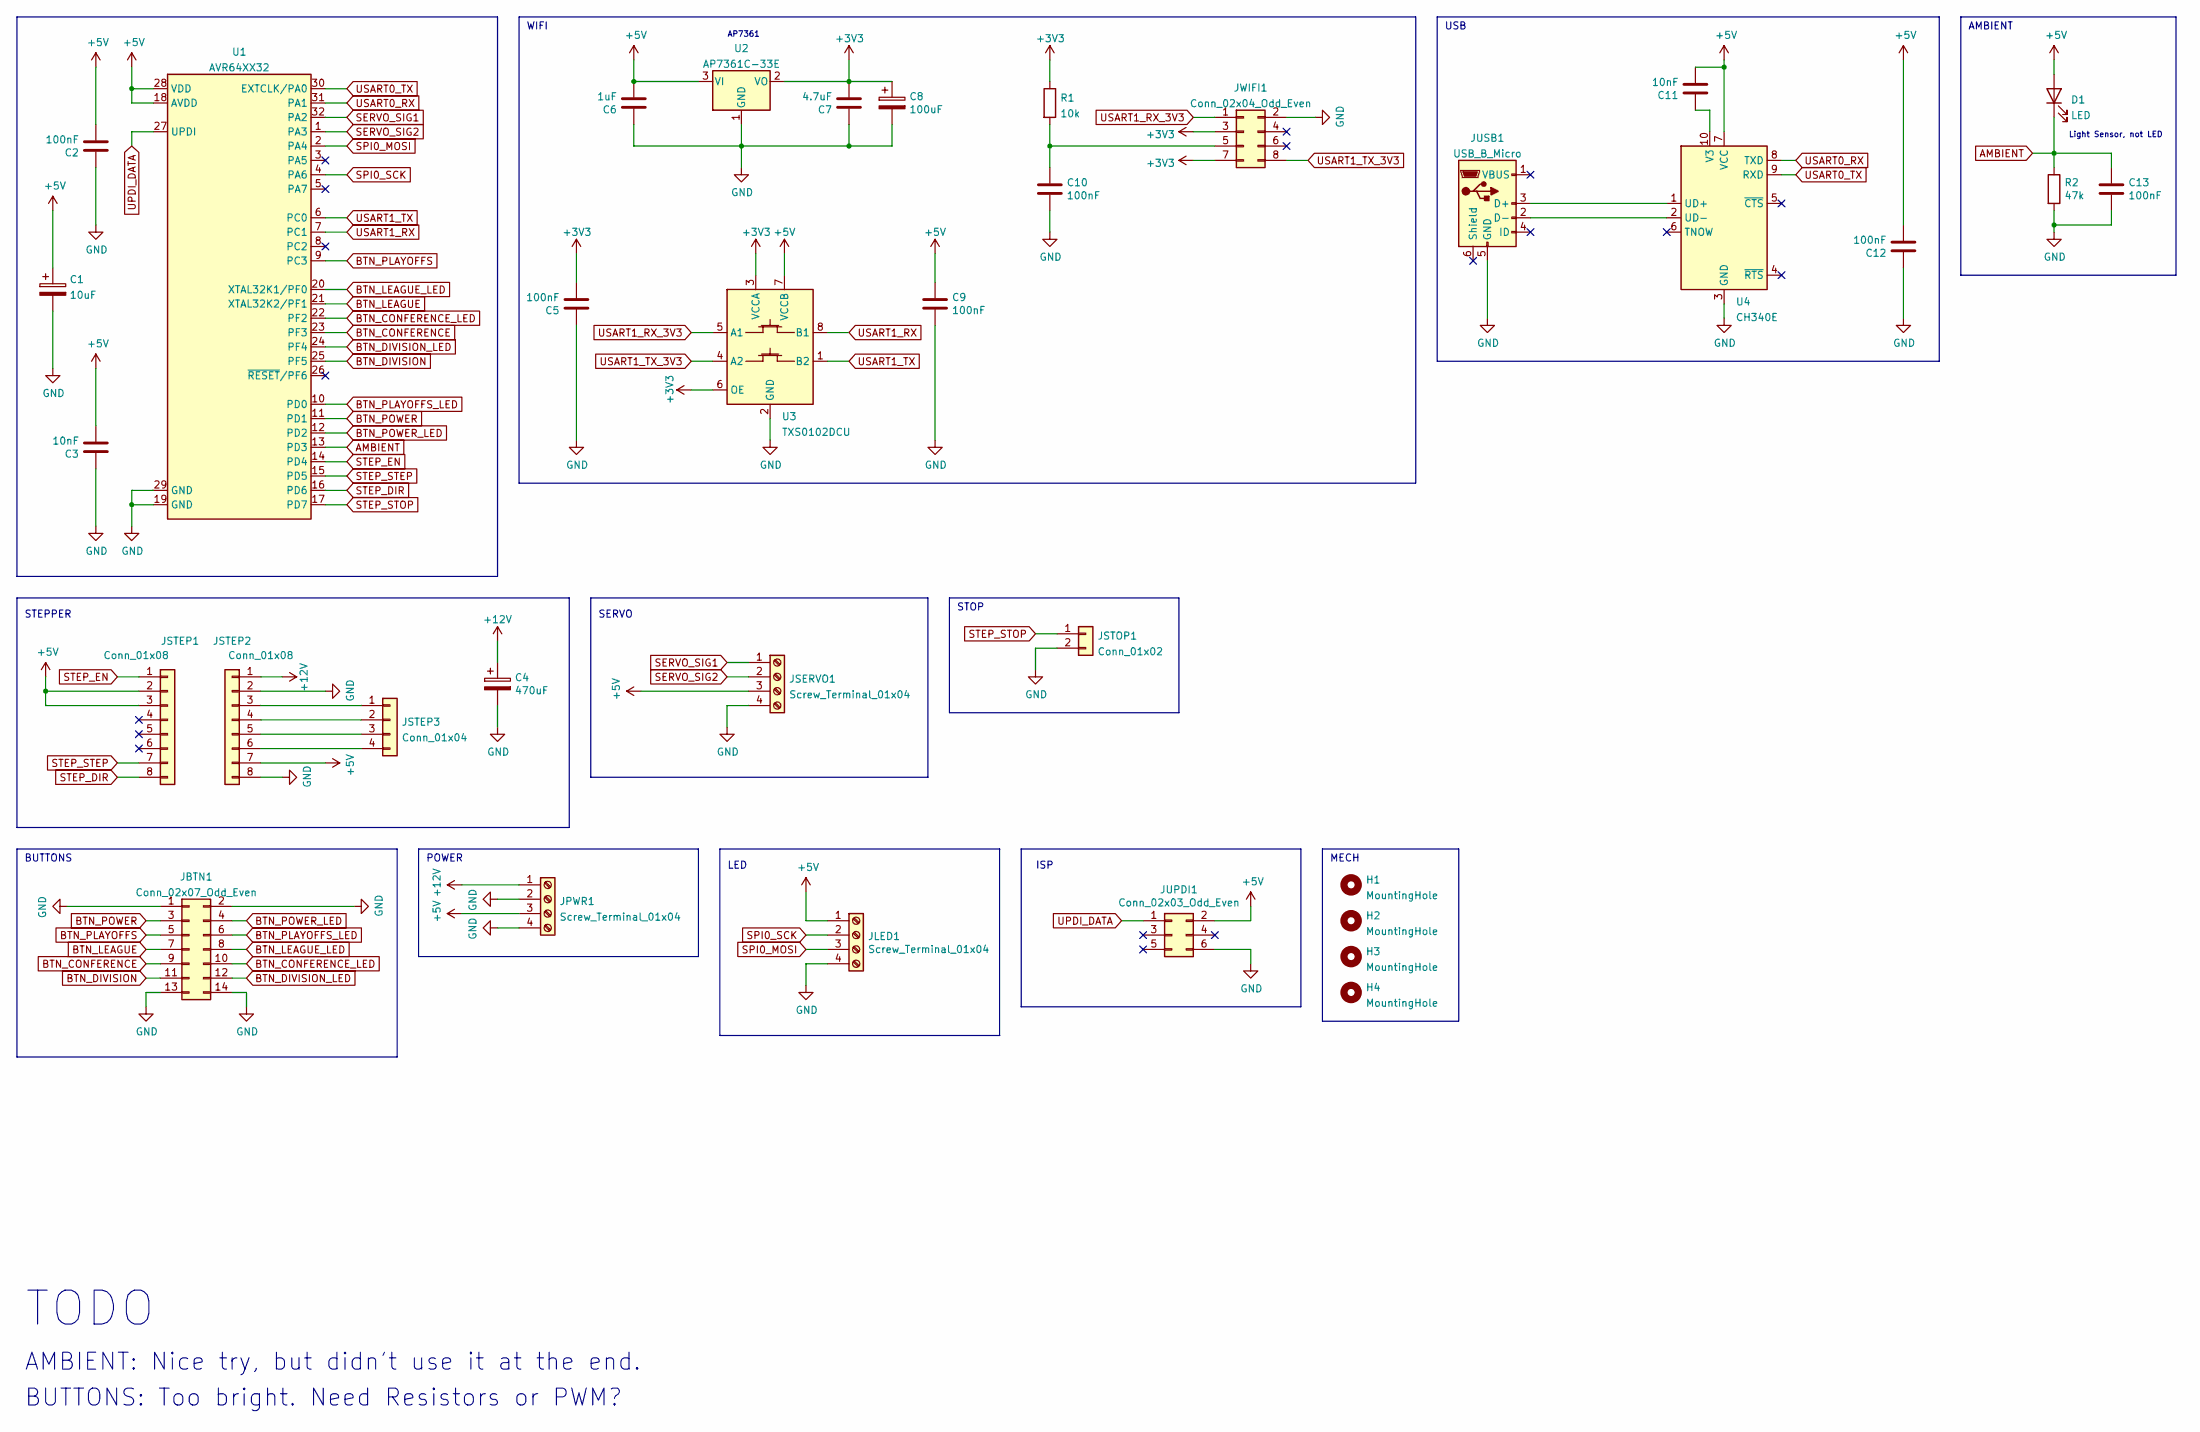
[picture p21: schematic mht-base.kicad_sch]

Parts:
C1: 10uF; CP_EIA-3216-18_Kemet-A
C2, C5, C9, C10, C12, C13: 100nF; C_0805_2012Metric
C3, C11: 10nF; C_0805_2012Metric
C4: 470uF; CP_Elec_8x10
C6: 1uF; C_0805_2012Metric
C7: 4.7uF; C_0805_2012Metric
C8: 100uF; CP_EIA-3528-21_Kemet-B
D1: LED; LED_D5.0mm
H1, H2, H3, H4: MountingHole; MountingHole_3.2mm_M3
JBTN1: Conn_02x07_Odd_Even; IDC-Header_2x07_P2.54mm_Vertical
JLED1: Screw_Terminal_01x04; TerminalBlock_RND_205-00047_1x04_P5.00mm_Horizontal
JPWR1: Screw_Terminal_01x04; TerminalBlock_RND_205-00047_1x04_P5.00mm_Horizontal
JSERVO1: Screw_Terminal_01x04; TerminalBlock_RND_205-00047_1x04_P5.00mm_Horizontal
JSTEP1, JSTEP2: Conn_01x08; PinSocket_1x08_P2.54mm_Vertical
JSTEP3: Conn_01x04; PinHeader_1x04_P2.54mm_Vertical
JSTOP1: Conn_01x02; TerminalBlock_RND_205-00012_1x02_P5.00mm_Horizontal
JUPDI1: Conn_02x03_Odd_Even; IDC-Header_2x03_P2.54mm_Vertical
JUSB1: USB_B_Micro; GCT-USB3076-30-A
JWIFI1: Conn_02x04_Odd_Even; PinHeader_2x04_P2.54mm_Vertical
R1: 10k; R_0805_2012Metric
R2: 47k; R_0805_2012Metric
U1: AVR64XX32; TQFP-32_7x7mm_P0.8mm
U2: AP7361C-33E; SOT-223-3_TabPin2
U3: TXS0102DCU; VSSOP-8_2.3x2mm_P0.5mm
U4: CH340E; MSOP-10_3x3mm_P0.5mm

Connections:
+3V3: C5.2, C7.2, C8.1, JWIFI1.3, JWIFI1.7, R1.1, U2.2 (VO), U3.3 (VCCA), U3.6 (OE)
+5V: C1.1, C2.2, C3.2, C6.2, C9.1, C11.2, C12.2, D1.2 (A), JLED1.1, JPWR1.3, JSERVO1.3, JSTEP1.2, JSTEP1.3, JSTEP2.7, JUPDI1.2, U1.18 (AVDD), U1.28 (VDD), U2.3 (VI), U3.7 (VCCB), U4.7 (VCC)
+12V: C4.1, JPWR1.1, JSTEP2.1
AMBIENT: C13.1, D1.1 (K), R2.1, U1.13 (PD3)
BTN_CONFERENCE: JBTN1.9, U1.23 (PF3)
BTN_CONFERENCE_LED: JBTN1.10, U1.22 (PF2)
BTN_DIVISION: JBTN1.11, U1.25 (PF5)
BTN_DIVISION_LED: JBTN1.12, U1.24 (PF4)
BTN_LEAGUE: JBTN1.7, U1.21 (XTAL32K2/PF1)
BTN_LEAGUE_LED: JBTN1.8, U1.20 (XTAL32K1/PF0)
BTN_PLAYOFFS: JBTN1.5, U1.9 (PC3)
BTN_PLAYOFFS_LED: JBTN1.6, U1.10 (PD0)
BTN_POWER: JBTN1.3, U1.11 (PD1)
BTN_POWER_LED: JBTN1.4, U1.12 (PD2)
GND: C1.2, C2.1, C3.1, C4.2, C5.1, C6.1, C7.1, C8.2, C9.2, C10.2, C12.1, C13.2, JBTN1.1, JBTN1.2, JBTN1.13, JBTN1.14, JLED1.4, JPWR1.2, JPWR1.4, JSERVO1.4, JSTEP2.2, JSTEP2.8, JSTOP1.2, JUPDI1.6, JUSB1.5 (GND), JWIFI1.2, R2.2, U1.19 (GND), U1.29 (GND), U2.1 (GND), U3.2 (GND), U4.3 (GND)
unnamed: C10.1, JWIFI1.5, R1.2
unnamed: C11.1, U4.10 (V3)
unnamed: JSTEP2.3, JSTEP3.1
unnamed: JSTEP2.4, JSTEP3.2
unnamed: JSTEP2.5, JSTEP3.3
unnamed: JSTEP2.6, JSTEP3.4
unnamed: JUSB1.2 (D-), U4.2 (UD-)
unnamed: JUSB1.3 (D+), U4.1 (UD+)
SERVO_SIG1: JSERVO1.1, U1.32 (PA2)
SERVO_SIG2: JSERVO1.2, U1.1 (PA3)
SPI0_MOSI: JLED1.3, U1.2 (PA4)
SPI0_SCK: JLED1.2, U1.4 (PA6)
STEP_DIR: JSTEP1.8, U1.16 (PD6)
STEP_EN: JSTEP1.1, U1.14 (PD4)
STEP_STEP: JSTEP1.7, U1.15 (PD5)
STEP_STOP: JSTOP1.1, U1.17 (PD7)
UPDI_DATA: JUPDI1.1, U1.27 (UPDI)
USART0_RX: U1.31 (PA1), U4.8 (TXD)
USART0_TX: U1.30 (EXTCLK/PA0), U4.9 (RXD)
USART1_RX: U1.7 (PC1), U3.8 (B1)
USART1_RX_3V3: JWIFI1.1, U3.5 (A1)
USART1_TX: U1.6 (PC0), U3.1 (B2)
USART1_TX_3V3: JWIFI1.8, U3.4 (A2)

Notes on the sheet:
TODO
USB
AMBIENT
LED
BUTTONS
STOP
WIFI
POWER
MECH
ISP
AP7361
STEPPER
AMBIENT: Nice try, but didn't use it at the end.
SERVO
Light Sensor, not LED
BUTTONS: Too bright. Need Resistors or PWM?

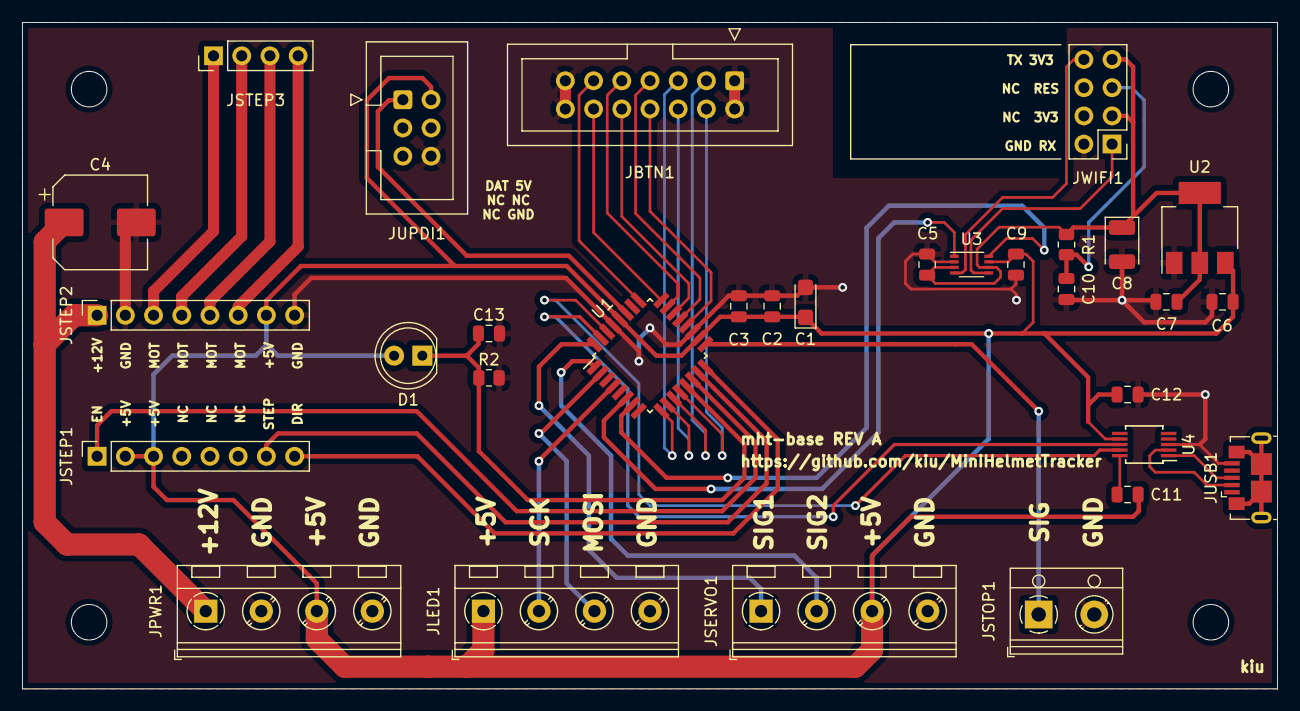
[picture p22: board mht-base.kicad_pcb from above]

Board: 2 copper layers, 113.0 x 60.0 mm, 35 parts (0 on the bottom side), 38 nets.

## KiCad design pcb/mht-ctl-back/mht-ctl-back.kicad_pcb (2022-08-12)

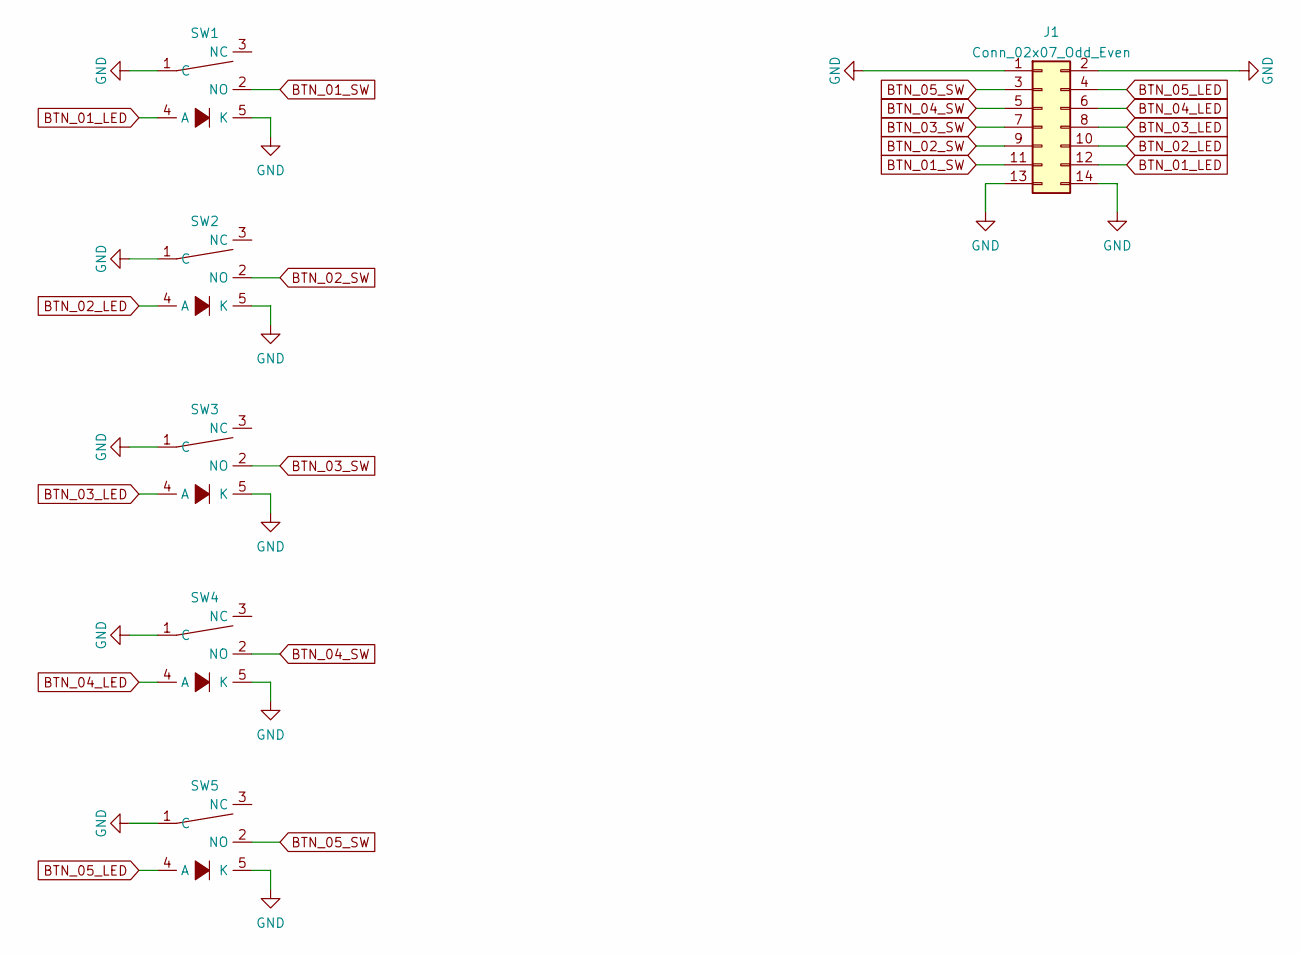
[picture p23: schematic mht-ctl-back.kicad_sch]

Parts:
J1: Conn_02x07_Odd_Even; IDC-Header_2x07_P2.54mm_Horizontal
SW1, SW2, SW3, SW4: PushButtonLED; PushButtonLED18
SW5: PushButtonLED; PushButtonLED24

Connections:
BTN_01_LED: J1.12, SW1.4 (A)
BTN_01_SW: J1.11, SW1.2 (NO)
BTN_02_LED: J1.10, SW2.4 (A)
BTN_02_SW: J1.9, SW2.2 (NO)
BTN_03_LED: J1.8, SW3.4 (A)
BTN_03_SW: J1.7, SW3.2 (NO)
BTN_04_LED: J1.6, SW4.4 (A)
BTN_04_SW: J1.5, SW4.2 (NO)
BTN_05_LED: J1.4, SW5.4 (A)
BTN_05_SW: J1.3, SW5.2 (NO)
GND: J1.1, J1.2, J1.13, J1.14, SW1.1 (C), SW1.5 (K), SW2.1 (C), SW2.5 (K), SW3.1 (C), SW3.5 (K), SW4.1 (C), SW4.5 (K), SW5.1 (C), SW5.5 (K)

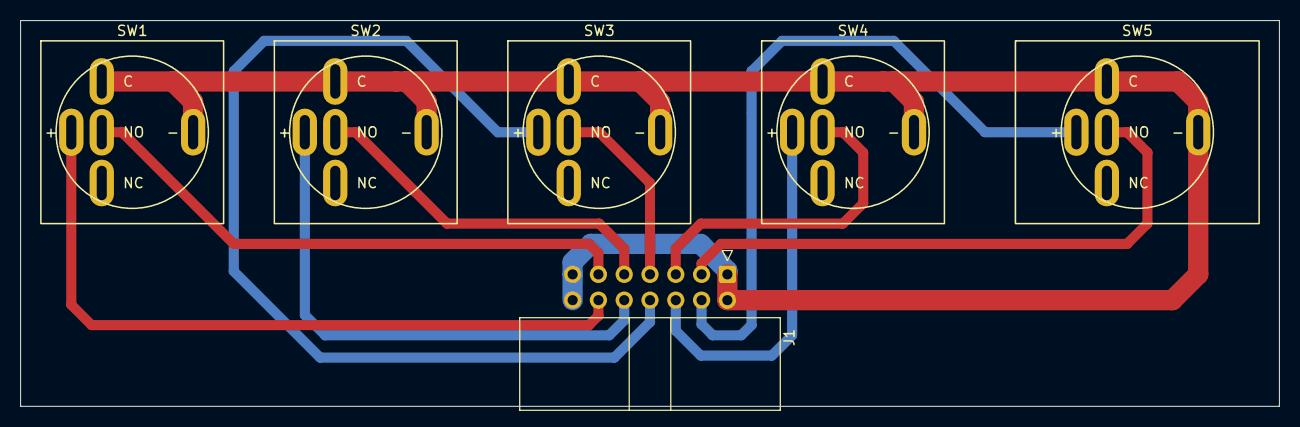
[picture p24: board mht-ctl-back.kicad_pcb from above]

Board: 2 copper layers, 124.0 x 38.0 mm, 6 parts (0 on the bottom side), 11 nets.

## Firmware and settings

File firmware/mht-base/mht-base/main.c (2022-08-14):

#include <atmel_start.h>
#include <stdio.h>
#include <string.h>
#include <util/delay.h>
#include "config.h"
#include "helmet.h"
#include "led.h"
#include "main.h"
#include "panic.h"
#include "servo.h"
#include "stepper.h"
#include "wifi.h"

opstate state = INIT;

volatile opmode mode = NONE;
volatile opmode modenext = NONE;
volatile opmode modelast = NONE;

volatile uint32_t seconds = 0;
volatile uint8_t ticked = true;

volatile uint8_t b_on = 0x00;
volatile uint8_t b_blink = 0x00;

uint8_t int_next = NONE;
uint8_t int_flag = 0x00;

uint8_t clean = 0;

const uint8_t CLEAN_FLAG = 0x42;

bool change_led_auto_tick = false;
bool led_state = true;

// -------------------------------------------------------------------------------

void main_change_led_auto(bool value) {
	led_state = value;
	change_led_auto_tick = true;
}

void main_button_update(opmode on, opmode blink) {
	b_on = (1 << on) | (1 << POWEROFF);
	b_on |= (1 << blink);
	
	b_blink = (1 << blink);
}

void main_set_unclean() {
	clean = 0x00;
}

opmode main_mode_get() {
	return mode;
}

opmode main_mode_next_get() {
	return modenext;
}

void main_mode_next_set(opmode om) {
	modenext = om;
}

// -------------------------------------------------------------------------------

char* main_mode_to_string(opmode mode) {
	if (mode == DIVISION) {
		return "DIVISION";
	}
	if (mode == CONFERENCE) {
		return "CONFERENCE";
	}
	if (mode == LEAGUE) {
		return "LEAGUE";
	}
	if (mode == PLAYOFFS) {
		return "PLAYOFFS";
	}
	if (mode == POWEROFF) {
		return "POWEROFF";
	}
	if (mode == NONE) {
		return "NONE";
	}
	return "UNKNOWN";
}

char* main_clean_to_string() {
	if (clean == CLEAN_FLAG) {
		return "CLEAN";
		} else {
		return "UNCLEAN";
	}
}

// -------------------------------------------------------------------------------

void main_store_load() {
	uint8_t storage[37];
	FLASH_0_read_eeprom_block(0, storage, 37);
	clean = storage[35];
	if (clean == CLEAN_FLAG) {
		uint8_t hc[35];
		memcpy(hc, storage, 35);
		helmet_set_current(hc);
	}
	modenext = storage[36];
	if (modenext == POWEROFF) {
		modenext = NONE;
	}
}

void main_store_save(opmode om) {
	printf("MAIN Storing configuration: %s / %s.\n", main_mode_to_string(om), main_clean_to_string());
	uint8_t storage[37];
	if (clean == CLEAN_FLAG) {
		memcpy(storage, helmet_get_current(), 35);
	}
	storage[35] = clean;
	storage[36] = om;
	FLASH_0_write_eeprom_block(0, storage, 37);
}

// -------------------------------------------------------------------------------


void main_tick() {
	
	if (change_led_auto_tick) {
		led_set_auto(led_state);
		change_led_auto_tick = false;
	}

	if (state != SHUTDOWN && mode != modenext) {
		if (modenext != POWEROFF) {
			modelast = modenext;
		}
		
		mode = modenext;
		main_button_update(mode, NONE);
		printf("MAIN Switching to mode: %s\n", main_mode_to_string(mode));
		
		if (mode == DIVISION) {
			helmet_set_mode(DIVISION);
		}
		if (mode == CONFERENCE) {
			helmet_set_mode(CONFERENCE);
		}
		if (mode == LEAGUE) {
			helmet_set_mode(LEAGUE);
		}
		if (mode == PLAYOFFS) {
			helmet_set_mode(PLAYOFFS);
		}

		if (mode == NONE) {
			led_blank();
		}

		if (mode == POWEROFF) {
			main_button_update(POWEROFF, POWEROFF);
			state = SHUTDOWN;
		}
	}

	if (state == INIT) {
		state = IDLE;
		return;
	}

	if (state == IDLE) {
		if (seconds % WIFI_RESET == 0) {
			wifi_reset();
			return;
		}
		if (seconds % WIFI_UPDATE == 0) {
			wifi_update();
			helmet_set_mode(mode);
			return;
		}
		if (!helmet_issort()) {
			printf("MAIN Sorting is needed, lets start.\n");
			state = SORTING;
			clean = 0x00;
			main_store_save(mode);
			helmet_set_mode(mode);
			return;
		}
	}

	if (state == SORTING) {
		if (helmet_dosort()) {
			printf("MAIN Sorting is completed.\n");
			state = IDLE;
			clean = CLEAN_FLAG;
			main_store_save(mode);
			return;
		}
	}
	
	if (state == SHUTDOWN) {
		return;
	}
}

// -------------------------------------------------------------------------------

ISR(PORTC_PORT_vect) {
	int_next = NONE;
	int_flag = PORTC.INTFLAGS;
	PORTC.INTFLAGS = 0xFF;
	
	if (int_flag & 1 << 3) {
		int_next = PLAYOFFS;
	}

	modenext = int_next;
	if (state != INIT && mode != POWEROFF) {
		main_button_update(mode, modenext);
	}
}

ISR(PORTD_PORT_vect) {
	int_next = NONE;
	int_flag = PORTD.INTFLAGS;
	PORTD.INTFLAGS = 0xFF;
	
	if (int_flag & 1 << 1) {
		int_next = POWEROFF;
	}

	modenext = int_next;
	if (state != INIT && mode != POWEROFF) {
		main_button_update(mode, modenext);
	}
}

ISR(PORTF_PORT_vect) {
	int_next = NONE;
	int_flag = PORTF.INTFLAGS;
	PORTF.INTFLAGS = 0xFF;
	
	if (int_flag & 1 << 1) {
		int_next = LEAGUE;
	}
	if (int_flag & 1 << 3) {
		int_next = CONFERENCE;
	}
	if (int_flag & 1 << 5) {
		int_next = DIVISION;
	}
	
	modenext = int_next;
	if (state != INIT && mode != POWEROFF) {
		main_button_update(mode, modenext);
	}
}

ISR(RTC_PIT_vect) {
	RTC.PITINTFLAGS = RTC_PI_bm;
	
	uint8_t out = b_on;
	
	if ((seconds & 0x01) == 1) {
		out = b_on & ~(b_blink);
	}

	if (!led_state) {
		out = 0x00;
	}
	
	BTN_DIVISION_LED_set_level((out >> 0) & 0x01);
	BTN_CONFERENCE_LED_set_level((out >> 1) & 0x01);
	BTN_LEAGUE_LED_set_level((out >> 2) & 0x01);
	BTN_PLAYOFFS_LED_set_level((out >> 3) & 0x01);
	BTN_POWER_LED_set_level((out >> 4) & 0x01);
	
	seconds++;
	ticked = true;
}

// -------------------------------------------------------------------------------

int main(void) {
	atmel_start_init();
	
	_delay_ms(2000);

	printf("\n");
	printf("mht-base v0.1 by kiu\n");
	printf("https://github.com/kiu/MiniHelmetTracker\n");
	printf("\n");

	_delay_ms(2000);

	sei();
	
	main_store_load();
	led_blank();
	
	if (ALWAYS_CLEAN) {
		clean = CLEAN_FLAG;
	}
	
	if (clean == CLEAN_FLAG) {
		printf("MAIN Previous shutdown was CLEAN, ready to start.\n");
		printf("MAIN Loaded layout:\n");
		helmet_print();
		printf("MAIN Last known mode: %s\n", main_mode_to_string(modenext));
		} else {
		printf("MAIN Previous shutdown was UNCLEAN, manual setup required.\n");
		helmet_load_manual();
		modenext = NONE;
		clean = CLEAN_FLAG;
		main_store_save(mode);
	}
	
	main_button_update(mode, modenext);

	servo_init();
	stepper_home();
	stepper_move(34);
	
	wifi_reset();
	wifi_update();
	
	while(state != SHUTDOWN) {
		if (ticked) {
			ticked = false;
			main_tick();
		}
		_delay_ms(10);
	}
	
	printf("MAIN Shutdown sequence initiated...\n");
	
	stepper_move(0);
	
	servo_shutdown();
	stepper_shutdown();
	
	clean = CLEAN_FLAG;
	main_store_save(modelast);

	led_blank();
	
	b_on = 0x00;
	
	printf("MAIN Shutdown completed. Go Seahawks.\n");
	
	_delay_ms(2000);
	
	cli();
}

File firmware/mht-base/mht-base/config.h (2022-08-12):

/*
* config.h
*
* Created: 22.07.2022 21:18:47
*  Author: kiu
*/

#ifndef CONFIG_H_
#define CONFIG_H_

// --------------------------------------------------

#define ALWAYS_CLEAN 0

// --------------------------------------------------

#define HELMET_DEBUG 1

// --------------------------------------------------

#define LED_ENABLE 1
#define LED_BRIGHTNESS 0x01

// --------------------------------------------------

#define SERVO_ENABLE 1

#define SERVO_DELAY 300
#define SERVO_PLATE_DOWN 32
#define SERVO_PLATE_MIDDLE 25
#define SERVO_PLATE_UP 18

#define SERVO_HORN_DOWN 17
#define SERVO_HORN_UP 28

// --------------------------------------------------

#define STEPPER_ENABLE 1

#define STEPPER_WIGGLE 400UL
#define STEPPER_OFFSET 2560UL
#define STEPPER_RAMP 1800UL

// SPEEDs are multiples of 10us

#define STEPPER_HOME_SPEED_FAST 20
#define STEPPER_HOME_SPEED_SLOW 160

#define STEPPER_SPEED_MIN 5 // 4
#define STEPPER_SPEED_FAST 0
#define STEPPER_SPEED_SLOW 20

#define STEPPER_SPEED_CHANGE (STEPPER_RAMP / (STEPPER_SPEED_SLOW - STEPPER_SPEED_FAST))

// --------------------------------------------------

#define WIFI_ENABLE 1
#define WIFI_DEBUG 0
#define WIFI_UPDATE 300UL
#define WIFI_RESET 21600UL

// --------------------------------------------------


#endif /* CONFIG_H_ */

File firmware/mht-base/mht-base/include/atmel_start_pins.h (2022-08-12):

/*
 * Code generated from START.
 *
 * This file will be overwritten when reconfiguring your START project.
 * Please copy examples or other code you want to keep to a separate file
 * to avoid losing it when reconfiguring.
 */
#ifndef ATMEL_START_PINS_H_INCLUDED
#define ATMEL_START_PINS_H_INCLUDED

#include <port.h>

/**
 * \brief Set PA0 pull mode
 *
 * Configure pin to pull up, down or disable pull mode, supported pull
 * modes are defined by device used
 *
 * \param[in] pull_mode Pin pull mode
 */
static inline void PA0_set_pull_mode(const enum port_pull_mode pull_mode)
{
	PORTA_set_pin_pull_mode(0, pull_mode);
}

/**
 * \brief Set PA0 data direction
 *
 * Select if the pin data direction is input, output or disabled.
 * If disabled state is not possible, this function throws an assert.
 *
 * \param[in] direction PORT_DIR_IN  = Data direction in
 *                      PORT_DIR_OUT = Data direction out
 *                      PORT_DIR_OFF = Disables the pin
 *                      (low power state)
 */
static inline void PA0_set_dir(const enum port_dir dir)
{
	PORTA_set_pin_dir(0, dir);
}

/**
 * \brief Set PA0 input/sense configuration
 *
 * Enable/disable PA0 digital input buffer and pin change interrupt,
 * select pin interrupt edge/level sensing mode
 *
 * \param[in] isc PORT_ISC_INTDISABLE_gc    = Iterrupt disabled but input buffer enabled
 *                PORT_ISC_BOTHEDGES_gc     = Sense Both Edges
 *                PORT_ISC_RISING_gc        = Sense Rising Edge
 *                PORT_ISC_FALLING_gc       = Sense Falling Edge
 *                PORT_ISC_INPUT_DISABLE_gc = Digital Input Buffer disabled
 *                PORT_ISC_LEVEL_gc         = Sense low Level
 */
static inline void PA0_set_isc(const PORT_ISC_t isc)
{
	PORTA_pin_set_isc(0, isc);
}

/**
 * \brief Set PA0 inverted mode
 *
 * Enable or disable inverted I/O on a pin
 *
 * \param[in] inverted true  = I/O on PA0 is inverted
 *                     false = I/O on PA0 is not inverted
 */
static inline void PA0_set_inverted(const bool inverted)
{
	PORTA_pin_set_inverted(0, inverted);
}

/**
 * \brief Set PA0 level
 *
 * Sets output level on a pin
 *
 * \param[in] level true  = Pin level set to "high" state
 *                  false = Pin level set to "low" state
 */
static inline void PA0_set_level(const bool level)
{
	PORTA_set_pin_level(0, level);
}

/**
 * \brief Toggle output level on PA0
 *
 * Toggle the pin level
 */
static inline void PA0_toggle_level()
{
	PORTA_toggle_pin_level(0);
}

/**
 * \brief Get level on PA0
 *
 * Reads the level on a pin
 */
static inline bool PA0_get_level()
{
	return PORTA_get_pin_level(0);
}

/**
 * \brief Set PA1 pull mode
 *
 * Configure pin to pull up, down or disable pull mode, supported pull
 * modes are defined by device used
 *
 * \param[in] pull_mode Pin pull mode
 */
static inline void PA1_set_pull_mode(const enum port_pull_mode pull_mode)
{
	PORTA_set_pin_pull_mode(1, pull_mode);
}

/**
 * \brief Set PA1 data direction
 *
 * Select if the pin data direction is input, output or disabled.
 * If disabled state is not possible, this function throws an assert.
 *
 * \param[in] direction PORT_DIR_IN  = Data direction in
 *                      PORT_DIR_OUT = Data direction out
 *                      PORT_DIR_OFF = Disables the pin
 *                      (low power state)
 */
static inline void PA1_set_dir(const enum port_dir dir)
{
	PORTA_set_pin_dir(1, dir);
}

/**
 * \brief Set PA1 input/sense configuration
 *
 * Enable/disable PA1 digital input buffer and pin change interrupt,
 * select pin interrupt edge/level sensing mode
 *
 * \param[in] isc PORT_ISC_INTDISABLE_gc    = Iterrupt disabled but input buffer enabled
 *                PORT_ISC_BOTHEDGES_gc     = Sense Both Edges
 *                PORT_ISC_RISING_gc        = Sense Rising Edge
 *                PORT_ISC_FALLING_gc       = Sense Falling Edge
 *                PORT_ISC_INPUT_DISABLE_gc = Digital Input Buffer disabled
 *                PORT_ISC_LEVEL_gc         = Sense low Level
 */
static inline void PA1_set_isc(const PORT_ISC_t isc)
{
	PORTA_pin_set_isc(1, isc);
}

/**
 * \brief Set PA1 inverted mode
 *
 * Enable or disable inverted I/O on a pin
 *
 * \param[in] inverted true  = I/O on PA1 is inverted
 *                     false = I/O on PA1 is not inverted
 */
static inline void PA1_set_inverted(const bool inverted)
{
	PORTA_pin_set_inverted(1, inverted);
}

/**
 * \brief Set PA1 level
 *
 * Sets output level on a pin
 *
 * \param[in] level true  = Pin level set to "high" state
 *                  false = Pin level set to "low" state
 */
static inline void PA1_set_level(const bool level)
{
	PORTA_set_pin_level(1, level);
}

/**
 * \brief Toggle output level on PA1
 *
 * Toggle the pin level
 */
static inline void PA1_toggle_level()
{
	PORTA_toggle_pin_level(1);
}

/**
 * \brief Get level on PA1
 *
 * Reads the level on a pin
 */
static inline bool PA1_get_level()
{
	return PORTA_get_pin_level(1);
}

/**
 * \brief Set SERVO_SIG1 pull mode
 *
 * Configure pin to pull up, down or disable pull mode, supported pull
 * modes are defined by device used
 *
 * \param[in] pull_mode Pin pull mode
 */
static inline void SERVO_SIG1_set_pull_mode(const enum port_pull_mode pull_mode)
{
	PORTA_set_pin_pull_mode(2, pull_mode);
}

/**
 * \brief Set SERVO_SIG1 data direction
 *
 * Select if the pin data direction is input, output or disabled.
 * If disabled state is not possible, this function throws an assert.
 *
 * \param[in] direction PORT_DIR_IN  = Data direction in
 *                      PORT_DIR_OUT = Data direction out
 *                      PORT_DIR_OFF = Disables the pin
 *                      (low power state)
 */
static inline void SERVO_SIG1_set_dir(const enum port_dir dir)
{
	PORTA_set_pin_dir(2, dir);
}

/**
 * \brief Set SERVO_SIG1 input/sense configuration
 *
 * Enable/disable SERVO_SIG1 digital input buffer and pin change interrupt,
 * select pin interrupt edge/level sensing mode
 *
 * \param[in] isc PORT_ISC_INTDISABLE_gc    = Iterrupt disabled but input buffer enabled
 *                PORT_ISC_BOTHEDGES_gc     = Sense Both Edges
 *                PORT_ISC_RISING_gc        = Sense Rising Edge
 *                PORT_ISC_FALLING_gc       = Sense Falling Edge
 *                PORT_ISC_INPUT_DISABLE_gc = Digital Input Buffer disabled
 *                PORT_ISC_LEVEL_gc         = Sense low Level
 */
static inline void SERVO_SIG1_set_isc(const PORT_ISC_t isc)
{
	PORTA_pin_set_isc(2, isc);
}

/**
 * \brief Set SERVO_SIG1 inverted mode
 *
 * Enable or disable inverted I/O on a pin
 *
 * \param[in] inverted true  = I/O on SERVO_SIG1 is inverted
 *                     false = I/O on SERVO_SIG1 is not inverted
 */
static inline void SERVO_SIG1_set_inverted(const bool inverted)
{
	PORTA_pin_set_inverted(2, inverted);
}
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

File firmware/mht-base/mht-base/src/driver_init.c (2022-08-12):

/**
 * \file
 *
 * \brief Driver initialization.
 *
 (c) 2020 Microchip Technology Inc. and its subsidiaries.

    Subject to your compliance with these terms,you may use this software and
    any derivatives exclusively with Microchip products.It is your responsibility
    to comply with third party license terms applicable to your use of third party
    software (including open source software) that may accompany Microchip software.

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
    IN NO EVENT WILL MICROCHIP BE LIABLE FOR ANY INDIRECT, SPECIAL, PUNITIVE,
    INCIDENTAL OR CONSEQUENTIAL LOSS, DAMAGE, COST OR EXPENSE OF ANY KIND
    WHATSOEVER RELATED TO THE SOFTWARE, HOWEVER CAUSED, EVEN IF MICROCHIP HAS
    BEEN ADVISED OF THE POSSIBILITY OR THE DAMAGES ARE FORESEEABLE. TO THE
    FULLEST EXTENT ALLOWED BY LAW, MICROCHIP'S TOTAL LIABILITY ON ALL CLAIMS IN
    ANY WAY RELATED TO THIS SOFTWARE WILL NOT EXCEED THE AMOUNT OF FEES, IF ANY,
    THAT YOU HAVE PAID DIRECTLY TO MICROCHIP FOR THIS SOFTWARE.
 *
 */

/*
 * Code generated by START.
 *
 * This file will be overwritten when reconfiguring your START project.
 * Please copy examples or other code you want to keep to a separate file
 * to avoid losing it when reconfiguring.
 */

#include "driver_init.h"
#include <system.h>

/* configure the pins and initialize the registers */
void USART_0_initialization(void)
{

	// Set pin direction to input
	PA1_set_dir(PORT_DIR_IN);

	PA1_set_pull_mode(
	    // <y> Pull configuration
	    // <id> pad_pull_config
	    // <PORT_PULL_OFF"> Off
	    // <PORT_PULL_UP"> Pull-up
	    PORT_PULL_OFF);

	// Set pin direction to output

	PA0_set_level(
	    // <y> Initial level
	    // <id> pad_initial_level
	    // <false"> Low
	    // <true"> High
	    false);

	PA0_set_dir(PORT_DIR_OUT);

	USART_0_init();
}

/* configure the pins and initialize the registers */
void USART_1_initialization(void)
{

	// Set pin direction to input
	PC1_set_dir(PORT_DIR_IN);

	PC1_set_pull_mode(
	    // <y> Pull configuration
	    // <id> pad_pull_config
	    // <PORT_PULL_OFF"> Off
	    // <PORT_PULL_UP"> Pull-up
	    PORT_PULL_OFF);

	// Set pin direction to output

	PC0_set_level(
	    // <y> Initial level
	    // <id> pad_initial_level
	    // <false"> Low
	    // <true"> High
	    false);

	PC0_set_dir(PORT_DIR_OUT);

	USART_1_init();
}

/* configure the pins and initialize the registers */
void SPI_0_initialization(void)
{

	// Set pin direction to input
	PA5_set_dir(PORT_DIR_IN);

	PA5_set_pull_mode(
	    // <y> Pull configuration
	    // <id> pad_pull_config
	    // <PORT_PULL_OFF"> Off
	    // <PORT_PULL_UP"> Pull-up
	    PORT_PULL_OFF);

	// Set pin direction to output

	PA4_set_level(
	    // <y> Initial level
	    // <id> pad_initial_level
	    // <false"> Low
	    // <true"> High
	    false);

	PA4_set_dir(PORT_DIR_OUT);

	// Set pin direction to output

	PA6_set_level(
	    // <y> Initial level
	    // <id> pad_initial_level
	    // <false"> Low
	    // <true"> High
	    false);

	PA6_set_dir(PORT_DIR_OUT);

	SPI_0_init();
}

void TIMER_0_initialization(void)
{

	TIMER_0_init();
}

/* Initialize registers */
void FLASH_0_initialization(void)
{
	FLASH_0_init();
}

void PWM_0_initialization(void)
{

	// Set pin direction to output

	SERVO_SIG1_set_level(
	    // <y> Initial level
	    // <id> pad_initial_level
	    // <false"> Low
	    // <true"> High
	    false);

	SERVO_SIG1_set_dir(PORT_DIR_OUT);

	PWM_0_init();
}

void PWM_1_initialization(void)
{

	// Set pin direction to output

	SERVO_SIG2_set_level(
	    // <y> Initial level
	    // <id> pad_initial_level
	    // <false"> Low
	    // <true"> High
	    false);

	SERVO_SIG2_set_dir(PORT_DIR_OUT);

	PWM_1_init();
}

/**
 * \brief System initialization
 */
void system_init()
{
	mcu_init();

	/* PORT setting on PC3 */

	BTN_PLAYOFFS_set_level(
	    // <y> Initial level
	    // <id> pad_initial_level
	    // <false"> Low
	    // <true"> High
	    false);

	BTN_PLAYOFFS_set_dir(
	    // <y> Pin direction
	    // <id> pad_dir
	    // <PORT_DIR_OFF"> Off
	    // <PORT_DIR_IN"> In
	    // <PORT_DIR_OUT"> Out
	    PORT_DIR_IN);

	BTN_PLAYOFFS_set_pull_mode(
	    // <y> Pull configuration
	    // <id> pad_pull_config
	    // <PORT_PULL_OFF"> Off
	    // <PORT_PULL_UP"> Pull-up
	    PORT_PULL_UP);

	BTN_PLAYOFFS_set_inverted(
	    // <y> Invert I/O on pin
	    // <id> pad_invert
	    // <false"> Not inverted
	    // <true"> Inverted
	    false);

	BTN_PLAYOFFS_set_isc(
	    // <y> Pin Input/Sense Configuration
	    // <id> pad_isc
	    // <PORT_ISC_INTDISABLE_gc"> Interrupt disabled but input buffer enabled
	    // <PORT_ISC_BOTHEDGES_gc"> Sense Both Edges
	    // <PORT_ISC_RISING_gc"> Sense Rising Edge
	    // <PORT_ISC_FALLING_gc"> Sense Falling Edge
	    // <PORT_ISC_INPUT_DISABLE_gc"> Digital Input Buffer disabled
	    // <PORT_ISC_LEVEL_gc"> Sense low Level
	    PORT_ISC_FALLING_gc);

	/* PORT setting on PD0 */

	// Set pin direction to output

	BTN_PLAYOFFS_LED_set_level(
	    // <y> Initial level
	    // <id> pad_initial_level
	    // <false"> Low
	    // <true"> High
	    true);

	BTN_PLAYOFFS_LED_set_dir(PORT_DIR_OUT);

	/* PORT setting on PD1 */

	BTN_POWER_set_level(
	    // <y> Initial level
	    // <id> pad_initial_level
	    // <false"> Low
	    // <true"> High
	    false);

	BTN_POWER_set_dir(
	    // <y> Pin direction
	    // <id> pad_dir
	    // <PORT_DIR_OFF"> Off
	    // <PORT_DIR_IN"> In
	    // <PORT_DIR_OUT"> Out
	    PORT_DIR_IN);

	BTN_POWER_set_pull_mode(
	    // <y> Pull configuration
	    // <id> pad_pull_config
	    // <PORT_PULL_OFF"> Off
	    // <PORT_PULL_UP"> Pull-up
	    PORT_PULL_UP);

	BTN_POWER_set_inverted(
	    // <y> Invert I/O on pin
	    // <id> pad_invert
	    // <false"> Not inverted
	    // <true"> Inverted
	    false);

	BTN_POWER_set_isc(
	    // <y> Pin Input/Sense Configuration
	    // <id> pad_isc
	    // <PORT_ISC_INTDISABLE_gc"> Interrupt disabled but input buffer enabled
	    // <PORT_ISC_BOTHEDGES_gc"> Sense Both Edges
	    // <PORT_ISC_RISING_gc"> Sense Rising Edge
	    // <PORT_ISC_FALLING_gc"> Sense Falling Edge
	    // <PORT_ISC_INPUT_DISABLE_gc"> Digital Input Buffer disabled
	    // <PORT_ISC_LEVEL_gc"> Sense low Level
	    PORT_ISC_FALLING_gc);

	/* PORT setting on PD2 */

	// Set pin direction to output

	BTN_POWER_LED_set_level(
	    // <y> Initial level
	    // <id> pad_initial_level
	    // <false"> Low
	    // <true"> High
	    true);

	BTN_POWER_LED_set_dir(PORT_DIR_OUT);

	/* PORT setting on PD4 */

	// Set pin direction to output

	STEP_EN_set_level(
	    // <y> Initial level
	    // <id> pad_initial_level
	    // <false"> Low
	    // <true"> High
	    true);

	STEP_EN_set_dir(PORT_DIR_OUT);

	/* PORT setting on PD5 */

	// Set pin direction to output

	STEP_STEP_set_level(
	    // <y> Initial level
	    // <id> pad_initial_level
	    // <false"> Low
	    // <true"> High
	    false);

	STEP_STEP_set_dir(PORT_DIR_OUT);

	/* PORT setting on PD6 */

	// Set pin direction to output
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

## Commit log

2022-08-12 Initial files.
    [chain-end.stl, chain-middle_4x.stl, chain-start.stl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]
2022-08-12 BOM and texts
    [bom-incomplete.ods, nfl_teams.csv]
2022-08-13 Need some waiting perios for servo to reach end position.
2022-08-14 Turn buttons off when leds are off
2022-08-19 35W model is good enough
    [mount-meanwell-35W.scad, mount-meanwell-35W.stl]
2022-09-08 Scores are null in case game didn't happen yet. Ignore those. If playoff didn't start yet, download is 400. Ignore this.
